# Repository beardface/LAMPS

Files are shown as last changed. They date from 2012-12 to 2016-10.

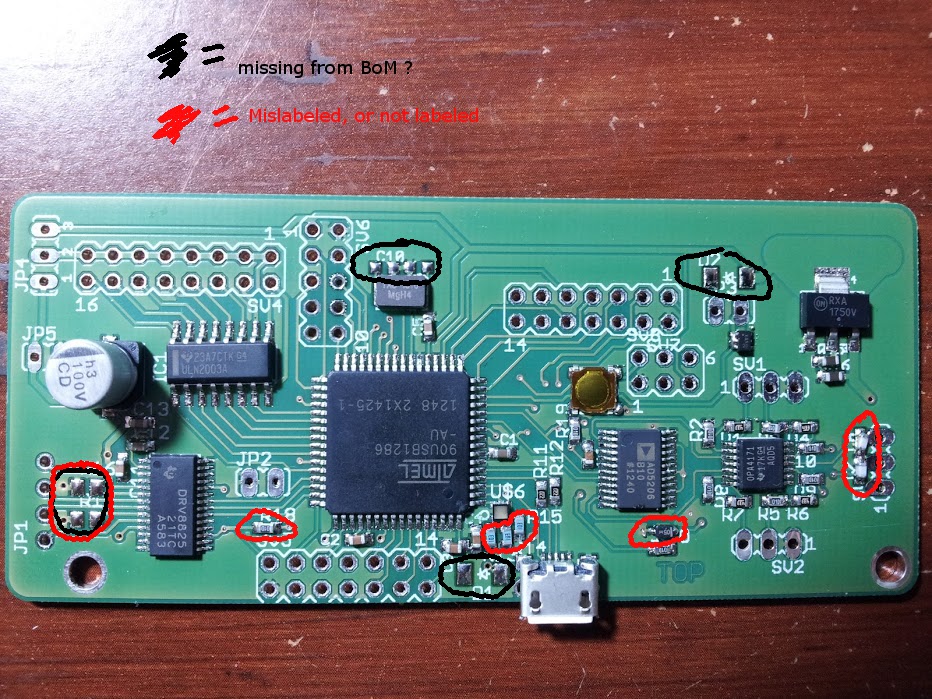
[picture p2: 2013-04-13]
pcb_design/OpenSL_1.0/board_review.jpg

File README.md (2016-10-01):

LAMPS - The Open Hardware SLA Printer
-------------------------------------
LAMPS (Laser Arduino Mega Pololu Shield|SLA Printer) is an open control board and SLA printer design.  The SLA Printer strives to be a low-cost, small footprint (It is only 200mmx350mm!), highly capable SLA Printer. The build platform size is currently 100mmx100mm, but could probably be increased by someone who is motivated to enhance the design.

#License
The schematic for the OpenSL electronics are licensed under the GPL.

The printer and its associated parts are licensed under the Creative Commons Attribution-NonCommercial-ShareAlike 3.0 Unported License.

Basically, use my design all you want! :) But, don't sell it.  If you want an exception, contact me.

#LAMPS Board
LAMPS is the PCB control board that rides on top of an Arduino Mega 2560.  It provides Galvanometer control (Through 12 bit DACs).  It also controls the laser, buttons, Z Stepper Motor (Through Pololu Carrier), End Stops, LEDs, etc...  (It is the Brainz).

Version 1.0 of the LAMPS board has been manufactured and tested... I found a few issues with the board and am currently redesigning and removing a few unnecessary components for 1.1. Release date T.B.D.

#Firmware
The firmware for LAMPS is a fork of Marlin (The best open source RepRap firmware I know of), and can be found here: https://github.com/beardface/Marlin-OpenSL
The firmware is very much an active work-in-progress, and I encourage you to fork, and contribute.

#LAMPS Printer Parts -WARNING... THIS IS NOT UP TO DATE-
All of the parts are available as sketchup (skp) and stl files.

##Printed Parts
* 1x [Laser Mount](https://github.com/beardface/LAMPS/blob/master/parts/lasermount.stl)
* 1x [Mirror Mount](https://github.com/beardface/LAMPS/blob/master/parts/mirrormount.stl)
* 4x [Vibrating Vat Mount](https://github.com/beardface/LAMPS/blob/master/parts/vibrating_vat_mount.stl)
* 1x [Z-Axis Top Mount](https://github.com/beardface/LAMPS/blob/master/parts/z_top_mount.stl)
* 1x [Z-Axis Bottom Mount](https://github.com/beardface/LAMPS/blob/master/parts/z_bottom_mount.stl)
* 1x [Build Platform Mount](https://github.com/beardface/LAMPS/blob/master/parts/platform_mount.stl)
* 1x [Build Stage](https://github.com/beardface/LAMPS/blob/master/parts/build_platform_connector.stl)
* 1x Endstop Mount

##Laser Cut Parts
###Platform
Use 3/16"-1/4" thick acrylic for the platforms.
* 1x [Vat Platform](https://github.com/beardface/LAMPS/blob/master/parts/top_platform.svg)
* 1x [Component Platform](https://github.com/beardface/LAMPS/blob/master/parts/bottom_platform.svg)
* 1x 80mmx80mm 1/4"Acryilc Stage Mount (leftover part from cutting of top_platform)

###VAT
Use 1/4" Clear (Transparent) Acrylic for the VAT!
* 1x [Vat Back](https://github.com/beardface/LAMPS/blob/master/parts/vat_design/vat_back.svg)
* 1x [Vat Front](https://github.com/beardface/LAMPS/blob/master/parts/vat_design/vat_front.svg)
* 1x [Vat Bottom](https://github.com/beardface/LAMPS/blob/master/parts/vat_design/vat_bottom.svg)
* 1x [Vat Handle](https://github.com/beardface/LAMPS/blob/master/parts/vat_design/vat_handle.svg)
* 2x [Vat Sides](https://github.com/beardface/LAMPS/blob/master/parts/vat_design/vat_side.svg)

##Non-Printed Parts
* 1x NEMA 17 Stepper Motor (Low Profile!)
* 2x 8mm Smooth Rod (~260mm)
* 1x 8mm Threaded Rod (~260mm) and 2-M8 nuts
* 4x LM8UU Bearings
* 1x LAMPS Electronics Kit (w/Pololu and 2x endstops)
* 1x LAMPS PCB Build Platform
* 1x LAMPS Musimi 2020 Rail Kit and connectors
  * 4x  350mm 2020 Extrusions w/end tapping holes
  * 11x 160mm 2020 Extrusions
  * 1x  110mm 2020 Extrusion
* 1x LAMPS Enclsoure & Hatch Kit
* 1x 405nm Laser (20mw-150mw) -- Build properties/cure time/etc... vary by laser!
* 1x 3" Square Mirror
* 1x Laser Galvo Set (20kpps) w/power supply
 * Resistance Configuration (Note to Self)
  * AXIS  |  SIZE     | GAIN      | LF         | HF        | LINEAR
  * X     |  4.96Kohm | 4.68 Kohm | 26.36 Kohm | 4.78 Kohm | 1.75 Kohm
  * Y     |  6.1Kohm  | 4.18 Kohm | 26.47 Kohm | 4.37 Kohm | 2.3 Kohm
* 1x +/-12V Power Supply (~1-3Amps)
* USB Cable
* Power Cable
* Screws, Nuts, Wires, Solder, Patience

##Optional (But Useful) Non-Printed Parts
* 1xLCD Screen
* 1xSD Card Reader (and corresponding circuit... T.B.D.)
* 1x Power Switch (110-250VAC), lighted
* 1x Power Terminal (Two combine power into single input)
* 1x 3-Prong Power Jack
 
###LAMPS IS A WORK IN PROGRESS.

##Some words of Caution
* Careful with 110-250VAC, it can --bite-- Seriously Harm you if you aren't careful
* Some 405nm Resins can be toxic while curing- take the appropriate measures to ensure you are working in a well ventelated room

~LAMPS design, details, and parts list are provided without any warranty or gaurantee- this is a community project, so lets work together to solve issues that may arise!

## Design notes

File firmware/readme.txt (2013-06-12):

Firmware can be found at:
http://github.com/Beardface/Marlin-OpenSL

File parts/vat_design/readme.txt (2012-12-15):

==Instructions==
Cut one of every part using 1/4" clear acrylic, except for vat_side.svg... you need two of those.

===Parts===
Vat Bottom (vat_bottom.svg) - Qty 1
Vat Side   (vat_side.svg)   - Qty 2
Vat Back   (vat_back.svg)   - Qty 1
Vat Front  (vat_front.svg)  - Qty 1
Vat Handle (vat_handle.svg) - Qty 1

*Glue all parts together, clamping as necessary.

*Once parts are glued together and vat has dried, use silicon to create a water tight seal on vat inside edges.

*You'll need to apply something (unkown) to the vat floor to prevent cured acrylic from sticking.

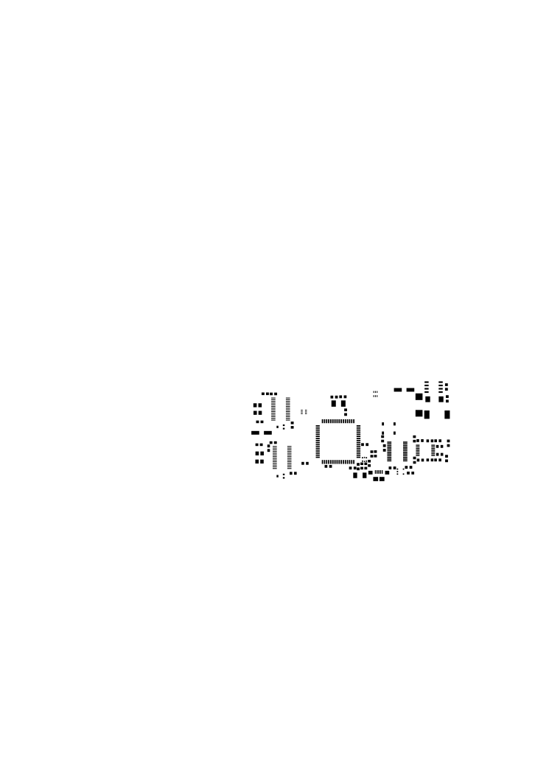
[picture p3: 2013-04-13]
pcb_design/OpenSL_1.0/usbl_stencil.png

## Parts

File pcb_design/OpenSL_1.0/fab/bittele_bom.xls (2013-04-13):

 | Open SL 1.0 – BOM – Pryntech
Item # | Ref Des | Description | Qty | Manufacturer | Mfg Part # | SMD count | THR count | FP count | Link
1 | U$1 | Processor | 1 | Atmel | AT90USB1286 | 1 |  |  | http://www.digikey.de/product-detail/de/AT90USB1286-AU/AT90USB1286-AU-ND/2238141
2 | U$7 U$11 | Stepper motor driver | 2 | Texas Instruments | DRV8825 |  |  | 2 | http://de.mouser.com/ProductDetail/Texas-Instruments/DRV8825PWP/?qs=sGAEpiMZZMvt6eWNl%252b39CONAp7d4Q4UX
3 | R16 R17 R22 R23 | Current sense resistor | 4 | Susumu | RL1220T-R050-J | 4 |  |  | http://www.digikey.de/product-detail/de/RL1220T-R050-J/RL12T.05JCT-ND/567358
4 | U$2 | Digital potentiometer | 1 | Analog Devices | AD5206BRUZ10-RL7 |  |  | 1 | http://www.digikey.de/product-detail/de/AD5206BRUZ10-RL7/AD5206BRUZ10-RL7CT-ND/3727008
5 | U$3 | Quad opamp | 1 | Texas Instruments | OPA4171 |  |  | 1 | http://de.mouser.com/ProductDetail/Texas-Instruments/OPA4171AIPW/
6 | U$4 | Crystal | 1 | TXC | 7A-16.000MAAJ-T | 1 |  |  | http://www.digikey.de/product-detail/de/7A-16.000MAAJ-T/887-1086-1-ND/2118963
7 | LASER, ENDA, ENDB, 24V | Connector screw term | 4 | TE Connectivity | 282834-2 |  | 4 |  | http://de.mouser.com/ProductDetail/TE-Connectivity-AMP/282834-2/
8 | MOTOR-A, MOTOR-B | Connector screw term | 2 | TE Connectivity | 282834-4 |  | 2 |  | http://de.mouser.com/ProductDetail/TE-Connectivity/282834-4/?qs=A%252bip%252bNCYi6Pqom9P%2faHyRQ%3d%3d
9 | +-15V XGAL YGAL | 1x3 0.1” header | 3 | FCI | 68001-203HLF |  | 3 |  | http://de.mouser.com/ProductDetail/FCI/68001-203HLF/
10 | U$40 | Switch regulator | 1 | Maxim | MAX5035BASA/V+ | 1 |  |  | http://de.mouser.com/ProductDetail/Maxim-Integrated/MAX5035BASA-V+/
11 | U$9 U$13 | MOSFET | 2 | Infineon | BSD816SNL6327 |  |  | 2 | http://de.mouser.com/ProductDetail/Infineon-Technologies/BSD816SN-L6327/?qs=sGAEpiMZZMskA%2fTOHXebNu3gKtDta7Pm
12 | U$14 | Linear regulator | 1 | On Semi | CAT6219-330TD-G | 1 |  |  | http://de.mouser.com/Search/ProductDetail.aspx
13 | U$6 | LED | 1 |  | LRTBR98G-R7T5-1+S7U-37+P7 | 1 |  |  | http://de.mouser.com/ProductDetail/Maxim-Integrated/MAX5035BASA-V+/
14 | U$8 U$12 | Potentiometer | 2 |  | PVZ3A103C01B00 | 2 |  |  | http://de.mouser.com/ProductDetail/Murata/PVZ3A103C01B00/?qs=sGAEpiMZZMvygUB3GLcD7pHHMwHWVspDJmsoKyelQV0%3d
15 | FAN, BOOT | 2x1 0.1” header | 2 | FCI | 68001-202H |  | 2 |  | http://de.mouser.com/ProductDetail/FCI/68001-202H/?qs=sGAEpiMZZMtsLRyDR9nM15lq0NThqwkGsPHYSk2petY%3d
16 | U$41 | Inductor | 1 | Bourns | SRU8043-101Y | 1 |  |  | http://www.digikey.de/product-detail/de/SRU8043-101Y/SRU8043-101YCT-ND/2353060
17 | D2 | Diode | 1 | ON Semi | MBRS2040LT3G | 1 |  |  | http://www.digikey.de/product-detail/de/MBRS2040LT3G/MBRS2040LT3GOSCT-ND/918004
18 | AUX2 | 2x5 0.1” header | 1 | FCI | 77313-802-10LF |  | 1 |  | http://de.mouser.com/ProductDetail/FCI/77313-802-10LF/
19 | R2 R3 R5 R8 R9 R10 R18 R19 R21 R24 | Resistor (100K) | 10 | Kamaya | WR06X1003FTL | 8 |  |  | http://de.mouser.com/ProductDetail/Kamaya/WR06X1003FTL/
20 | C14 C32 | Bulk capacitor | 2 | Panasonic | EEE-FPV101XAP | 2 |  |  | http://www.digikey.de/product-detail/de/EEE-FPV101XAP/PCE4554CT-ND/1701053
21 | C31 | Output capacitor | 1 | Kemet | T495D686M010ATE150 | 1 |  |  | http://de.mouser.com/ProductDetail/Kemet/T495D686M010ATE150/
22 | R11 R12 | Resistor (22R) | 2 | Bourns | CR0603-FX-22R0ELF | 2 |  |  | http://de.mouser.com/ProductDetail/Bourns/CR0603-FX-22R0ELF/?qs=sGAEpiMZZMu61qfTUdNhG6LqqFhkr6pU9bwfCpAqbTI%3d
23 | D1 | Diode | 1 | ON Semi | MBR0520LT1G | 1 |  |  | http://www.digikey.de/product-detail/de/MBR0520LT1G/MBR0520LT1GOSCT-ND/917965
24 | R1 R4 R6 R7 R13 R14 R15 | Resistor (43K) | 7 | Bourns (http://de.mouser.com/bourns) | CR0603-FX-4302ELF (http://de.mouser.com/ProductDetail/Bourns/CR0603-FX-4302ELF/) | 7 |  |  | http://de.mouser.com/ProductDetail/Bourns/CR0603-FX-4302ELF/
25 | C3 C18 C19 | MLCC | 3 | TDK | C1608X6S1A106M | 3 |  |  | http://de.mouser.com/ProductDetail/TDK/C1608X6S1A106M/
26 | C2 C4 C5 C6 C7 C8 C11 C13 C15 C17 C20 C29 C30 | MLCC | 13 | TDK | C1608Y5V1H104Z | 13 |  |  | http://de.mouser.com/ProductDetail/TDK/C1608Y5V1H104Z/?qs=sGAEpiMZZMvQvaS66kI3TvHonbvhj0AsH45N8eLStt8%3d
27 | C12 C16 | MLCC (0.01u) | 2 | TDK | CGA5L4C0G2J103J | 2 |  |  | http://de.mouser.com/ProductDetail/TDK/CGA5L4C0G2J103J/?qs=sGAEpiMZZMs5EsmM6MQhfRRHRow8fGba
28 | C1 | MLCC | 1 | Vishay/Vitramon | VJ0603V105MXQPW1BC | 1 |  |  | http://de.mouser.com/ProductDetail/Vishay-Vitramon/VJ0603V105MXQPW1BC/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
29 | U$10 | Push button | 1 | E-Switch | TL3315NF250Q | 1 |  |  | http://www.digikey.de/product-detail/de/TL3315NF250Q/EG4622CT-ND/1870402
30 | AUX1 | 2x7 0.1” header | 2 | FCI | 67997-114HLF |  | 2 |  | http://de.mouser.com/ProductDetail/FCI/67997-114HLF/
31 | ICSP | 2x3 0.1” header | 1 | FCI | 67996-206HLF |  | 1 |  | http://de.mouser.com/ProductDetail/FCI/67996-206HLF/
32 | C9 C10 | MLCC | 2 | Murata | GRM1885C1H180FA01J | 2 |  |  | http://de.mouser.com/ProductDetail/Murata/GRM1885C1H180FA01J/
33 | U$5 | USB connector | 1 | FCI | 10118193-0001LF | 1 |  |  | http://de.mouser.com/Search/ProductDetail.aspx

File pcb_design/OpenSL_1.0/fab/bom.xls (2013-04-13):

Line item | Count | PN | Cost/100 | Cost/ea | Cost/50 | Cost/ea | Cost/25 | Cost/ea | RD | Description | Value | Package | Ratings | Mnft | Source | SMD count | THR count | FP count | LL count | Link
1 | 1 | AT90USB1286 | 503.45 | 5.0345 | 285.68 | 5.7136 | 142.84 | 5.7136 | U$1 | Processor |  | TQFP-64 |  | Atmel | digikey | 1 |  |  |  | http://www.digikey.de/product-detail/de/AT90USB1286-AU/AT90USB1286-AU-ND/2238141
2 | 2 | DRV8825 | 602 | 6.02 | 302 | 6.04 | 208 | 8.32 | U$7 U$11 | Stepper motor driver |  |  |  | Texas Instruments | mouser |  |  | 2 |  | http://de.mouser.com/ProductDetail/Texas-Instruments/DRV8825PWP/?qs=sGAEpiMZZMvt6eWNl%252b39CONAp7d4Q4UX
3 | 4 | RL1220T-R050-J | 53.07 | 0.5307 | 34.12 | 0.6824 | 17.06 | 0.6824 | R16 R17 R22 R23 | Current sense resistor | 0.05R | R0805 | 5% 1/4W | Susumu | digikey | 4 |  |  |  | http://www.digikey.de/product-detail/de/RL1220T-R050-J/RL12T.05JCT-ND/567358
4 | 1 | AD5206BRUZ10-RL7 | 315.89 | 3.1589 | 173.66 | 3.4732 | 86.83 | 3.4732 | U$2 | Digital potentiometer | 10k | TSSOP24 |  | Analog Devices | digikey |  |  | 1 |  | http://www.digikey.de/product-detail/de/AD5206BRUZ10-RL7/AD5206BRUZ10-RL7CT-ND/3727008
5 | 1 | OPA4171 | 112 | 1.12 | 83.5 | 1.67 | 41.75 | 1.67 | U$3 | Quad opamp |  | TSSOP14 |  | Texas Instruments | mouser |  |  | 1 |  | http://de.mouser.com/ProductDetail/Texas-Instruments/OPA4171AIPW/
6 | 1 | 7A-16.000MAAJ-T | 45.02 | 0.4502 | 28.2 | 0.564 | 14.1 | 0.564 | U$4 | Crystal | 16mhz |  | 30ppm, 18pf | TXC | digikey | 1 |  |  |  | http://www.digikey.de/product-detail/de/7A-16.000MAAJ-T/887-1086-1-ND/2118963
7 | 4 | 282834-2 | 312.4 | 3.124 | 156.2 | 3.124 | 78.1 | 3.124 |  | Connector screw term |  |  |  | TE Connectivity | mouser |  | 4 |  |  | http://de.mouser.com/ProductDetail/TE-Connectivity-AMP/282834-2/
8 | 2 | 282834-4 | 109 | 1.09 | 63.5 | 1.27 | 31.75 | 1.27 |  | Connector screw term |  |  |  | TE Connectivity | mouser |  | 2 |  |  | http://de.mouser.com/ProductDetail/TE-Connectivity/282834-4/?qs=A%252bip%252bNCYi6Pqom9P%2faHyRQ%3d%3d
9 | 3 | 68001-203HLF | 20.6 | 0.206 | 10.3 | 0.206 | 5.5 | 0.22 | +-15V XGAL YGAL | 1x3 0.1” header |  |  |  | FCI | mouser |  | 3 |  |  | http://de.mouser.com/ProductDetail/FCI/68001-203HLF/
10 | 1 | MAX5035BASA/V+ | 199 | 1.99 | 99.5 | 1.99 | 68.75 | 2.75 | U$40 | Switch regulator |  |  |  | Maxim | mouser | 1 |  |  |  | http://de.mouser.com/ProductDetail/Maxim-Integrated/MAX5035BASA-V+/
11 | 2 | BSD816SNL6327 | 40.4 | 0.404 | 20.2 | 0.404 | 11.85 | 0.474 | U$9 U$13 | MOSFET |  |  |  | Infineon | mouser |  |  | 2 |  | http://de.mouser.com/ProductDetail/Infineon-Technologies/BSD816SN-L6327/?qs=sGAEpiMZZMskA%2fTOHXebNu3gKtDta7Pm
12 | 1 | CAT6219-330TD-G | 34.6 | 0.346 | 18.15 | 0.363 | 9.08 | 0.3632 | U$14 | Linear regulator |  |  |  | On Semi | mouser | 1 |  |  |  | http://de.mouser.com/Search/ProductDetail.aspx
13 | 1 | LRTBR98G-R7T5-1+S7U-37+P7 | 45.2 | 0.452 | 23.95 | 0.479 | 12.83 | 0.5132 | U$6 | LED |  |  |  |  |  | 1 |  |  |  | http://de.mouser.com/ProductDetail/Maxim-Integrated/MAX5035BASA-V+/
14 | 2 | PVZ3A103C01B00 | 26.2 | 0.262 | 13.1 | 0.262 | 10.5 | 0.42 | U$8 U$12 | Potentiometer |  |  |  |  |  | 2 |  |  |  | http://de.mouser.com/ProductDetail/Murata/PVZ3A103C01B00/?qs=sGAEpiMZZMvygUB3GLcD7pHHMwHWVspDJmsoKyelQV0%3d
15 | 2 | 68001-202H | 10.4 | 0.104 | 5.2 | 0.104 | 2.9 | 0.116 |  | 2x1 0.1” header |  |  |  | FCI | mouser |  | 2 |  |  | http://de.mouser.com/ProductDetail/FCI/68001-202H/?qs=sGAEpiMZZMtsLRyDR9nM15lq0NThqwkGsPHYSk2petY%3d
16 | 1 | SRU8043-101Y | 55.1 | 0.551 | 29.85 | 0.597 | 17.23 | 0.6892 | U$41 | Inductor |  |  |  | Bourns | digikey | 1 |  |  |  | http://www.digikey.de/product-detail/de/SRU8043-101Y/SRU8043-101YCT-ND/2353060
17 | 1 | MBRS2040LT3G | 48 | 0.48 | 23.99 | 0.4798 | 14.72 | 0.5888 | D2 | Diode |  | DO214AA |  | ON Semi | digikey | 1 |  |  |  | http://www.digikey.de/product-detail/de/MBRS2040LT3G/MBRS2040LT3GOSCT-ND/918004
18 | 1 | 77313-802-10LF | 31 | 0.31 | 15.5 | 0.31 | 7.75 | 0.31 |  | 2x5 0.1” header |  |  |  | FCI | mouser |  | 1 |  |  | http://de.mouser.com/ProductDetail/FCI/77313-802-10LF/
19 | 10 | WR06X1003FTL | 7 | 0.07 | 3.5 | 0.07 | 2 | 0.08 | R2 R3 R5 R8 R9 R10 R18 R19 R21 R24 | Resistor | 100k | R0603 | 1.00% | Kamaya | mouser | 8 |  |  |  | http://de.mouser.com/ProductDetail/Kamaya/WR06X1003FTL/
20 | 2 | EEE-FPV101XAP | 88 | 0.88 | 43.99 | 0.8798 | 24.44 | 0.9776 | C14 C32 | Bulk capacitor | 100u | Panasonic D |  | Panasonic | digikey | 2 |  |  |  | http://www.digikey.de/product-detail/de/EEE-FPV101XAP/PCE4554CT-ND/1701053
21 | 1 | T495D686M010ATE150 | 62.7 | 0.627 | 34.65 | 0.693 | 17.33 | 0.6932 | C31 | Output capacitor | 68u | D/7343-31R |  | Kemet | mouser | 1 |  |  |  | http://de.mouser.com/ProductDetail/Kemet/T495D686M010ATE150/
22 | 2 | CR0603-FX-22R0ELF | 2.2 | 0.022 | 2.2 | 0.044 | 2.2 | 0.088 | R11 R12 | Resistor | 22R | R0603 | 1.00% | Bourns | mouser | 2 |  |  |  | http://de.mouser.com/ProductDetail/Bourns/CR0603-FX-22R0ELF/?qs=sGAEpiMZZMu61qfTUdNhG6LqqFhkr6pU9bwfCpAqbTI%3d
23 | 1 | MBR0520LT1G | 15.21 | 0.1521 | 9.78 | 0.1956 | 4.89 | 0.1956 | D1 | Diode |  | SOD-123 |  | ON Semi | digikey | 1 |  |  |  | http://www.digikey.de/product-detail/de/MBR0520LT1G/MBR0520LT1GOSCT-ND/917965
24 | 7 |  | 6.6 | 0.066 | 4.4 | 0.088 | 2.2 | 0.088 | R1 R4 R6 R7 R13 R14 R15 | Resistor | 43k | R0603 | 1.00% |  | mouser | 7
25 | 3 | C1608X6S1A106M | 40.4 | 0.404 | 20.2 | 0.404 | 15 | 0.6 | C3 C18 C19 | MLCC | 10u | C0603 | 10V | TDK | mouser | 3 |  |  |  | http://de.mouser.com/ProductDetail/TDK/C1608X6S1A106M/
26 | 13 | C1608Y5V1H104Z | 6 | 0.06 | 4 | 0.08 | 2 | 0.08 | C2 C4 C5 C6 C7 C8 C11 C13 C15 C17 C20 C29 C30 | MLCC | 0.1u | C0603 | 50V | TDK | mouser | 13 |  |  |  | http://de.mouser.com/ProductDetail/TDK/C1608Y5V1H104Z/?qs=sGAEpiMZZMvQvaS66kI3TvHonbvhj0AsH45N8eLStt8%3d
27 | 2 |  | 6.2 | 0.062 | 3 | 0.06 | 2 | 0.08 | C12 C16 | MLCC | 0.01u | C0603 |  |  |  | 2
28 | 1 | VJ0603V105MXQPW1BC | 90 | 0.9 | 45 | 0.9 | 20 | 0.8 | C1 | MLCC | 1u | C0603 | 10V | Vishay/Vitramon | mouser | 1 |  |  |  | http://de.mouser.com/ProductDetail/Vishay-Vitramon/VJ0603V105MXQPW1BC/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
29 | 1 | TL3315NF250Q | 13.95 | 0.1395 | 7.38 | 0.1476 | 3.83 | 0.1532 | U$10 | Push button |  |  |  | E-Switch | digikey | 1 |  |  |  | http://www.digikey.de/product-detail/de/TL3315NF250Q/EG4622CT-ND/1870402
30 | 2 | 67997-114HLF | 74.4 | 0.744 | 37.2 | 0.744 | 20.2 | 0.808 |  | 2x7 0.1” header |  |  |  | FCI | mouser |  | 2 |  |  | http://de.mouser.com/ProductDetail/FCI/67997-114HLF/
31 | 1 | 67996-206HLF | 15.7 | 0.157 | 8 | 0.16 | 4 | 0.16 |  | 2x3 0.1” header |  |  |  | FCI | mouser |  | 1 |  |  | http://de.mouser.com/ProductDetail/FCI/67996-206HLF/
32 | 2 | GRM1885C1H180FA01J | 6.2 | 0.062 | 3 | 0.06 | 2 | 0.08 | C9 C10 | MLCC | 18pF | C0603 | 10V | Murata | mouser | 2 |  |  |  | http://de.mouser.com/ProductDetail/Murata/GRM1885C1H180FA01J/
33 | 1 | 10118193-0001LF | 24.8 | 0.248 | 12.8 | 0.256 | 6.4 | 0.256 | U$5 | USB connector |  |  |  | FCI | mouser | 1 |  |  |  | http://de.mouser.com/Search/ProductDetail.aspx
34
35
36
total | 80 | 0 | 3022.69 | 30.2269 | 1625.7 | 32.514 | 910.03 | 36.4012 |  |  |  |  |  |  |  | 57 | 15 | 6 | 0

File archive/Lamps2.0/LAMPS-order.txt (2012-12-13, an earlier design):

Order list for C:/Users/Justin/eagle/LAMPS/Lamps2.0/LAMPS.sch
Exported from EAGLE with DesignLink

Quantity	Value	Package	Order code	Manufacturer	Manuf. Code	Availability	Price (from)	Description
1	7906	TO220V	94M7930		KA7906TU	1087	0.279	FAIRCHILD SEMICONDUCTOR - KA7906TU - IC, V REG -6.0V, 7906, TO-220-3
6		1X02	unknown					
4		1X01	unknown					
1	MSTBA2	MSTBA2	71C4161	FARNELL	1757242	351	0.318	PHOENIX CONTACT - 1757242 - PIN HEADER, 2POS, 5.08MM
1	MSTBA4	MSTBA4	unknown					
1	MSTBA3	MSTBA3	71C4162	FARNELL	1757255	211	0.802	PHOENIX CONTACT - 1757255 - TERMINAL BLOCK, PCB, 3 POS
4		1X04	unknown					
2	M04X2	2X4	unknown					
3	0.1uF	C2.5-2	unknown					
1	100nF	C0805	unknown					
2	1uF	C2.5-2	unknown					
2	100uF	153CLV-0605	unknown					
2	1N4004	DO41-10	unknown					
1	MFR500	MFR500	unknown					
5		3PIN-HEADER	unknown					
1	7805TV	TO220V	unknown					
1	TLV5618	SOCKET-08	76C8920	TEXAS INSTRUMENT CONNECTORS	TLV5618AIP	13	7.52	TEXAS INSTRUMENTS - TLV5618AIP - IC, DAC, 12BIT, 93KSPS, DIP-8
2	TL082P	DIL08	unknown					
1	7806TV	TO220V	unknown					
1		2X03	unknown					
1		2X05	unknown					
3		CHIP-LED0805	unknown					
2	STP55NF06L	TO220BV	63J7168	INTERNATIONAL RECTIFIER(IR)	IRF1010EZPBF	2723	0.848	INTERNATIONAL RECTIFIER - IRF1010EZPBF - N CHANNEL MOSFET, 60V, 75A TO-220AB
1	20k	B25P	unknown					
7	100k	R0805	unknown					
3	1k	B25P	unknown					
5	10k	R0805	unknown					
3	1K	R0805	unknown					
1	10r	R0805	unknown					
1	10r	M0805	unknown					
4	200k	R0805	unknown					
2	4.7K	R0805	unknown					
2	1.8K	R0805	unknown					
1		B3F-31XX	unknown					
2	THAT1646	THAT1646	50M5186		THAT1646P08-U	1	3.39	THAT CORPORATION - THAT1646P08-U - IC, BALANCED LINE DRIVER, DIP-8
1	A4988BREAKOUT	A4988BREAKOUT	unknown					
1	ARDUINO_MEGA_SHIELD	ARDUINO_MEGA_SHIELD	unknown

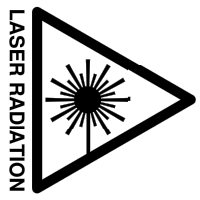
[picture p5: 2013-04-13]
parts/OpenSL/LaserCut/LC_LaserMount/laser_warning_90.png

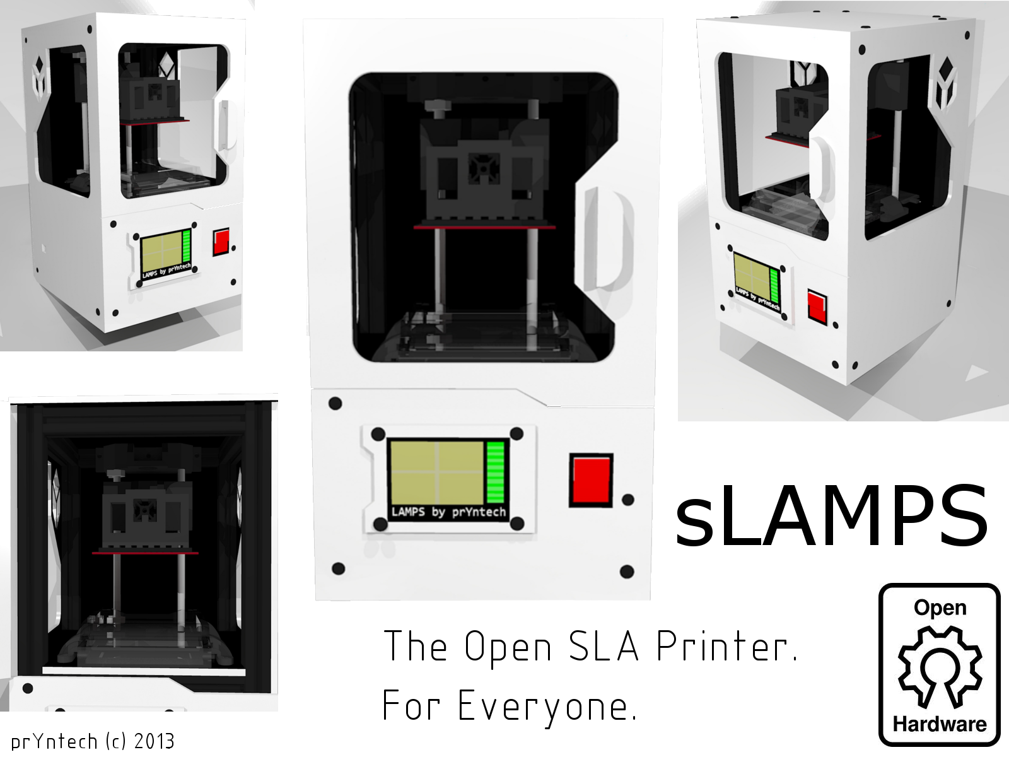
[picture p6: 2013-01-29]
parts/rendering/sLAMPS_Flyer.png

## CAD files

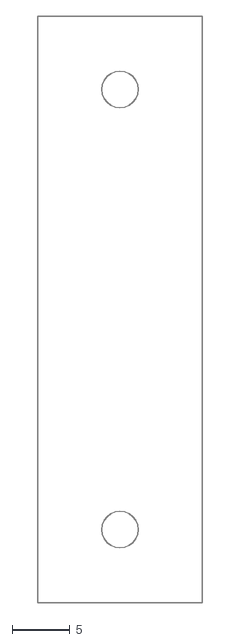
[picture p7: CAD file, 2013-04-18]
parts/2.0_plastic/vat_mount_new.dxf
14.2 x 50.8

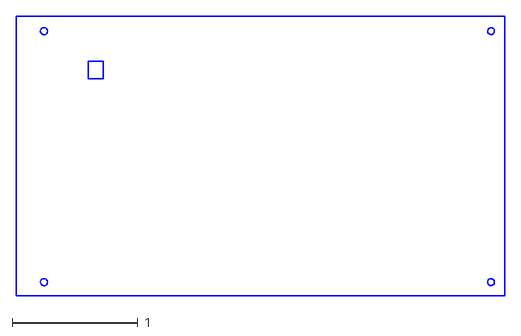
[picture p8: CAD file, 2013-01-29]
parts/case_design/dxf/clear_window/clear_side_window_two.dxf
3.89 x 2.22

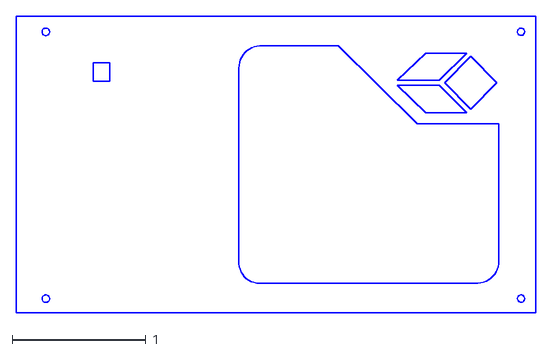
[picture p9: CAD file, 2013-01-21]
parts/case_design/dxf/left_side.dxf
3.89 x 2.22

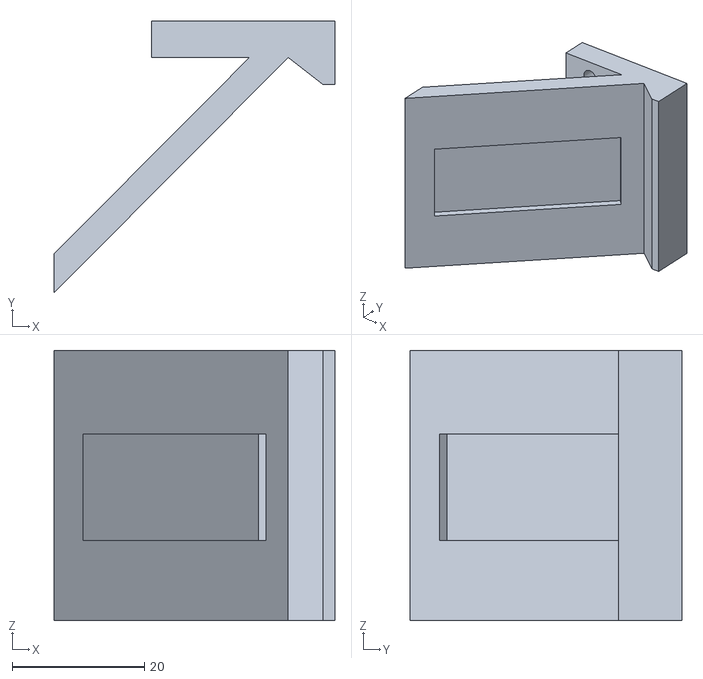
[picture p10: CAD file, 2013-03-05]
parts/Mirror_Mount.stl
42.5 x 41.1 x 40.9

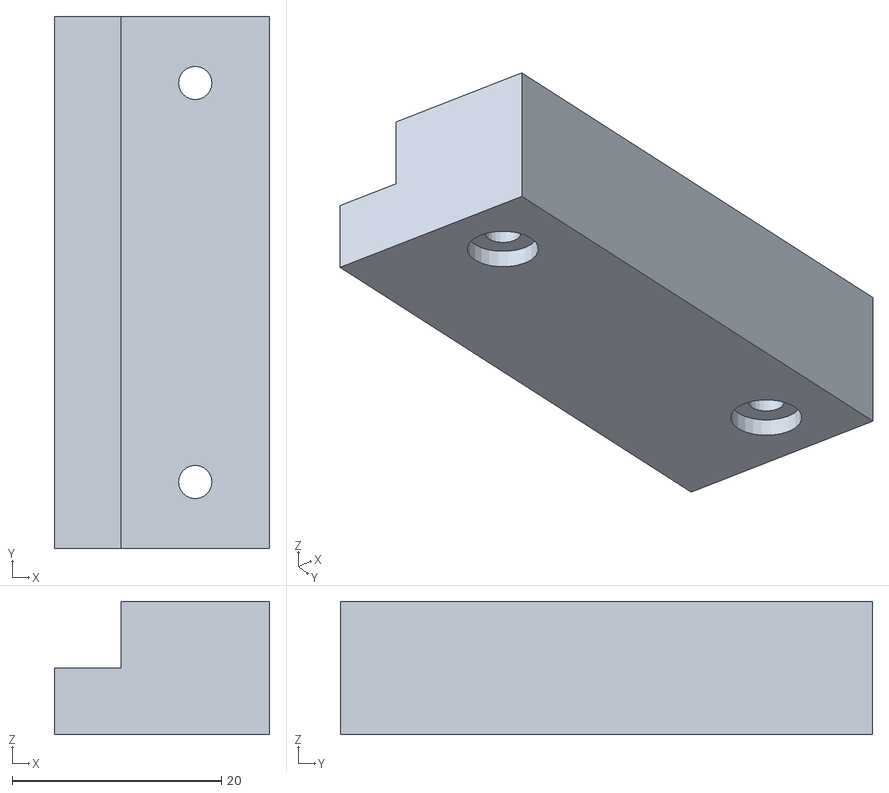
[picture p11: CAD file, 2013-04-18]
parts/OpenSL/3DPrinted/vat_mount.stl
20.5 x 50.8 x 12.7

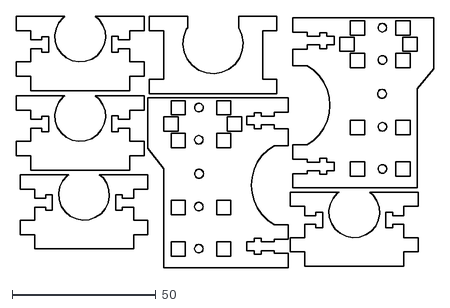
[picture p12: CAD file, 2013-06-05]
parts/OpenSL/LaserCut/DXF/laser_mount.DXF
145.2 x 87.5

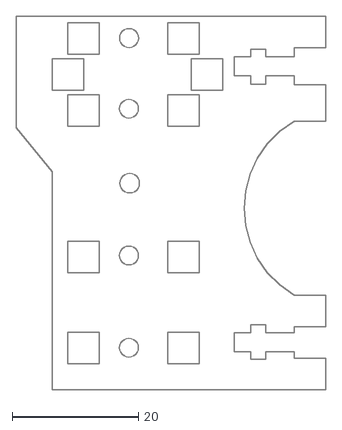
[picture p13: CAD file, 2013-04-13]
parts/OpenSL/LaserCut/LC_LaserMount/laser_mount_3.dxf
49.0 x 59.2

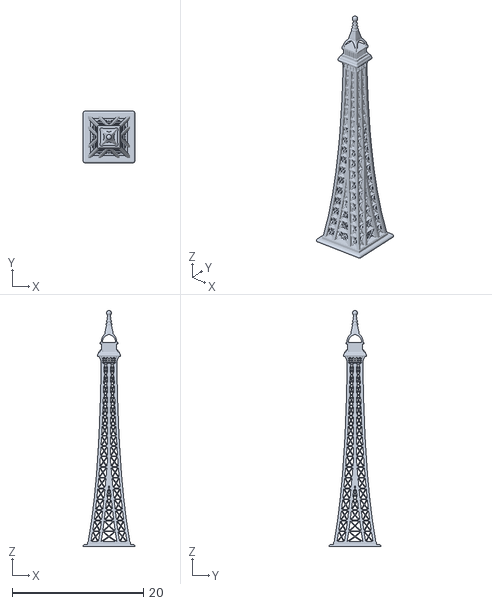
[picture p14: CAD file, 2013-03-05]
parts/tests/EiffelTower_top.stl
7.87 x 7.87 x 36.0

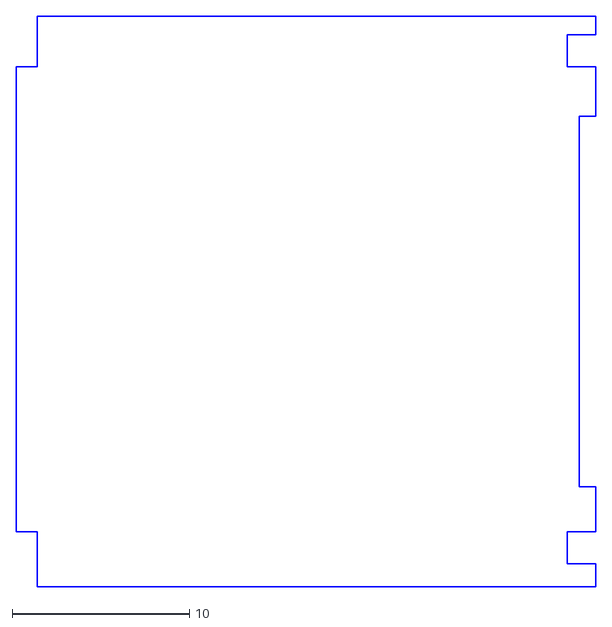
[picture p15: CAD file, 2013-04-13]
parts/vat_design/vat_bottom_test_2.dxf
32.7 x 32.2

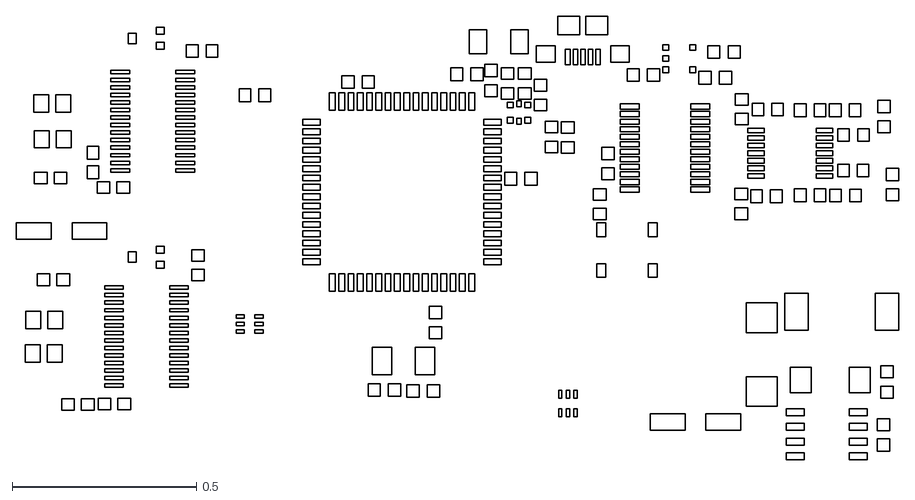
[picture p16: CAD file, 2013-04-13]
pcb_design/OpenSL_1.0/usb3l.dxf
2.39 x 1.20

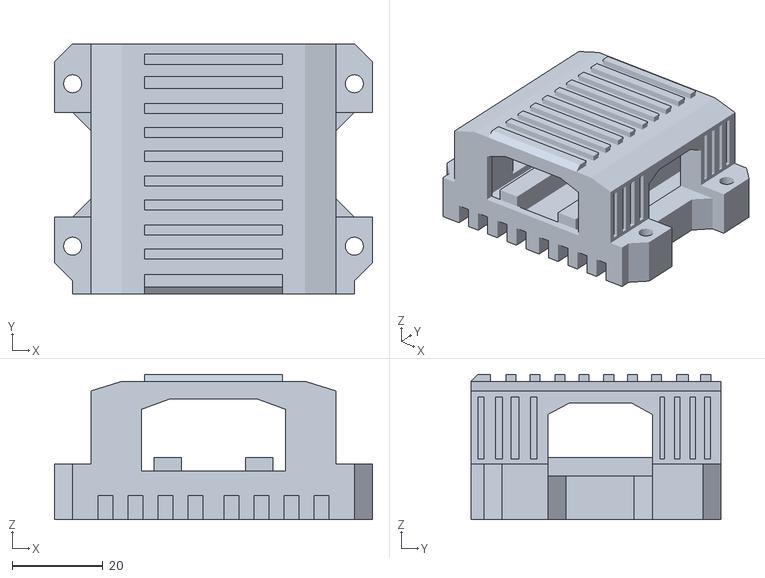
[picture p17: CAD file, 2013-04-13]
parts/2.0_plastic/platform_head.stl
70.1 x 55.2 x 32.1

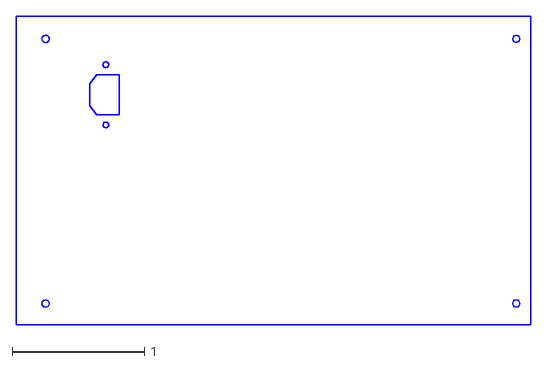
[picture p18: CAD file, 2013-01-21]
parts/case_design/dxf/back.dxf
3.89 x 2.33

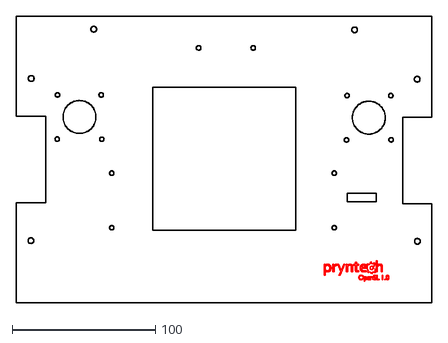
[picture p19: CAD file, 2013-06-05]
parts/OpenSL/LaserCut/DXF/top_platform.DXF
290.1 x 200.0

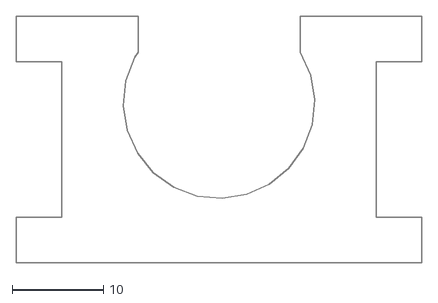
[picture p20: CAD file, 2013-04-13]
parts/OpenSL/LaserCut/LC_LaserMount/laser_mount_2.dxf
44.4 x 27.0

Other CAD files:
parts/tests/vat_adherence_30mm_square.stl
parts/vat_design/vat_bottom_test.dxf
parts/vat_mount.stl
parts/2.0_plastic/laser_mount_2.0.stl
parts/2.0_plastic/platform_base.stl
parts/2.0_plastic/vat_mount_new.skp
parts/Archive/Build_Platform.stl
parts/Archive/LaserAndPrinted/DXF/bottom_platform.DXF
parts/Archive/LaserAndPrinted/DXF/z_mount_left.DXF
parts/Archive/LaserAndPrinted/DXF/z_mount_right.DXF
parts/Archive/LaserAndPrinted/LC_LaserMount/laser_mount_1.dxf
parts/Archive/LaserAndPrinted/laser_mount_2.0.stl
parts/Archive/LaserAndPrinted/platform_base.stl
parts/Archive/LaserAndPrinted/vat_mount_new.skp
parts/Archive/Laser_Mount.stl
parts/Archive/Laser_Mount_Iris.stl
parts/Archive/Vat/vat_back.dxf
parts/Archive/Vat/vat_bottom.dxf
parts/Archive/Vat/vat_bottom_test.dxf
parts/Archive/Vat/vat_front.dxf
parts/Archive/Vat/vat_handle.dxf
parts/Archive/Vat/vat_side.dxf
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

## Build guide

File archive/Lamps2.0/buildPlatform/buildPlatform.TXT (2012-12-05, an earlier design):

%
M48
M72
T01C0.0630
T02C0.0866
%
T01
X1164Y3133
X3133Y1164
X5101Y1164
X7070Y1164
X11991Y1164
X13960Y1164
X15928Y1164
X19865Y1164
X21834Y1164
X23802Y1164
X28723Y1164
X30692Y1164
X32660Y1164
X34629Y3133
X34629Y5101
X34629Y7070
X34629Y11991
X34629Y13960
X34629Y15928
X34629Y19865
X34629Y21834
X34629Y23802
X34629Y28723
X34629Y30692
X34629Y32660
X32660Y34629
X30692Y34629
X28723Y34629
X23802Y34629
X21834Y34629
X19865Y34629
X15928Y34629
X13960Y34629
X11991Y34629
X7070Y34629
X5101Y34629
X3133Y34629
X1164Y32660
X1164Y30692
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

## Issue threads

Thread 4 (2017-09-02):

Purchase hardware

superdave42, 2017-09-02:
Is there any way to purchase this assembled. Just the DAC interface board?

DonVitosurf, 2018-01-16:
I would also like to buy it.

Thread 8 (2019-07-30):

about the STL modle and data in www.pryntech.com

BigYuanHead, 2019-07-30:
hello, I have great interest in this project, but emmmm....unfortunately, I can just get limited information in github, like PCB and its firmware, could you please send me more losed data, such as its assemble guide and STL model...... so that I can complete this machine?? thank you ^-^

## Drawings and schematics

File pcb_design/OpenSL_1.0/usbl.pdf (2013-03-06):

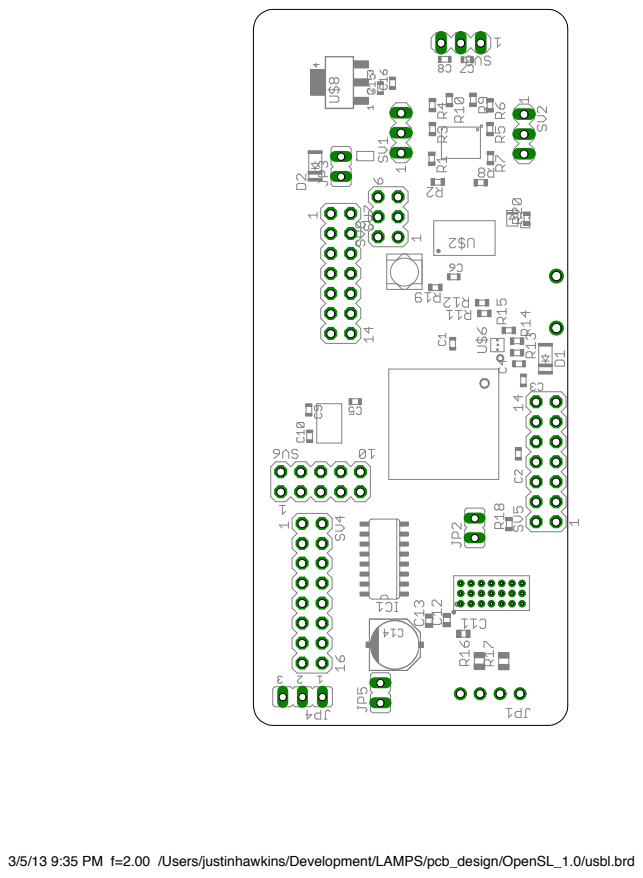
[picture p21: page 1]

3/5/13 9:35 PM f=2.00 /Users/justinhawkins/Development/LAMPS/pcb_design/OpenSL_1.0/usbl.brd

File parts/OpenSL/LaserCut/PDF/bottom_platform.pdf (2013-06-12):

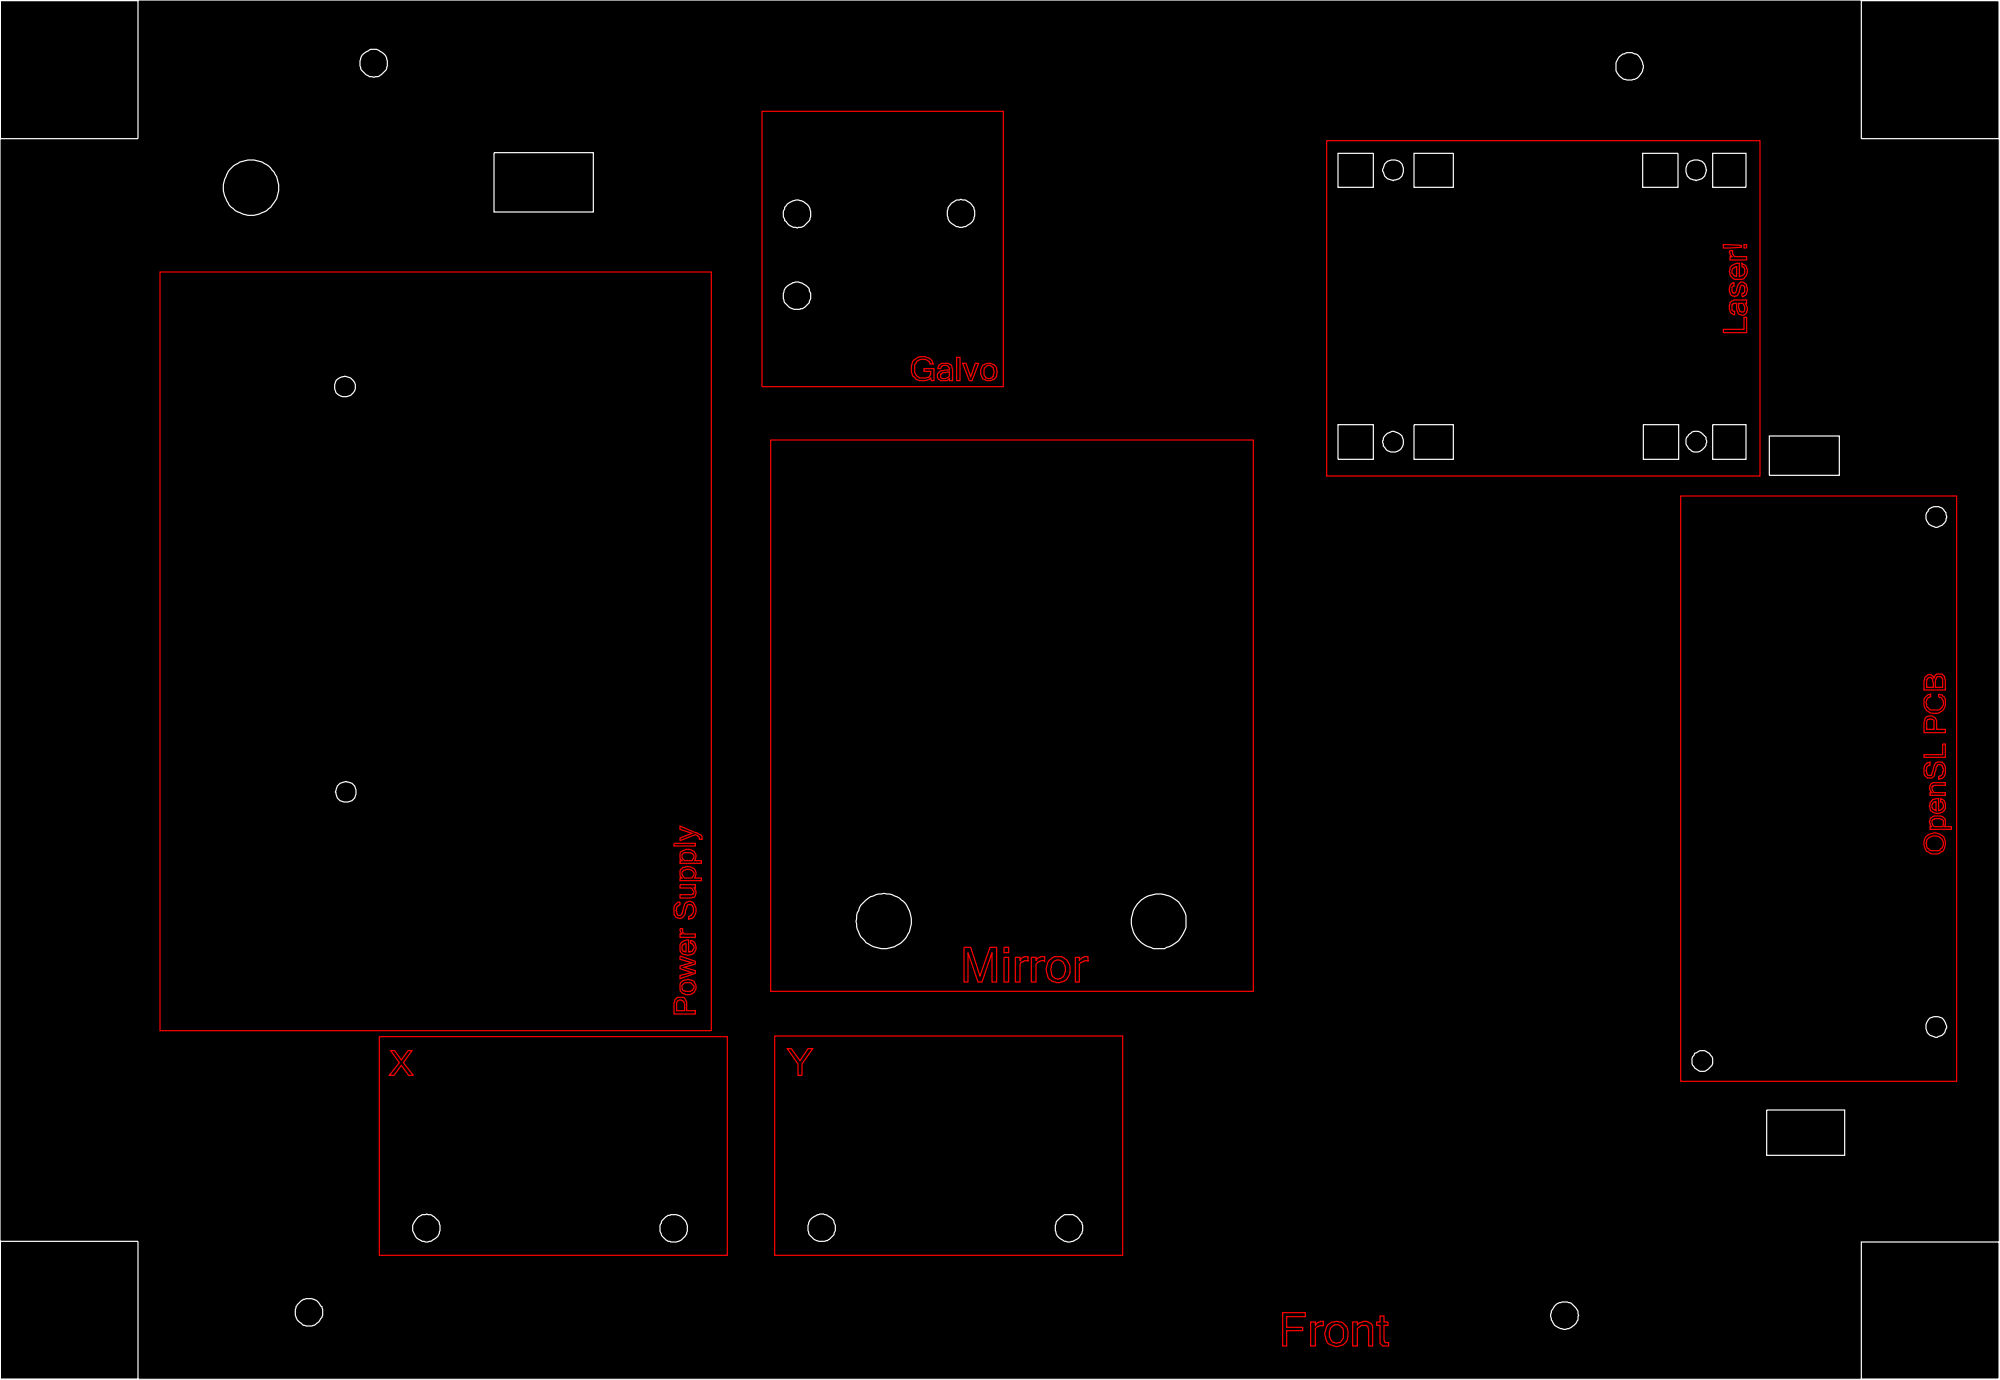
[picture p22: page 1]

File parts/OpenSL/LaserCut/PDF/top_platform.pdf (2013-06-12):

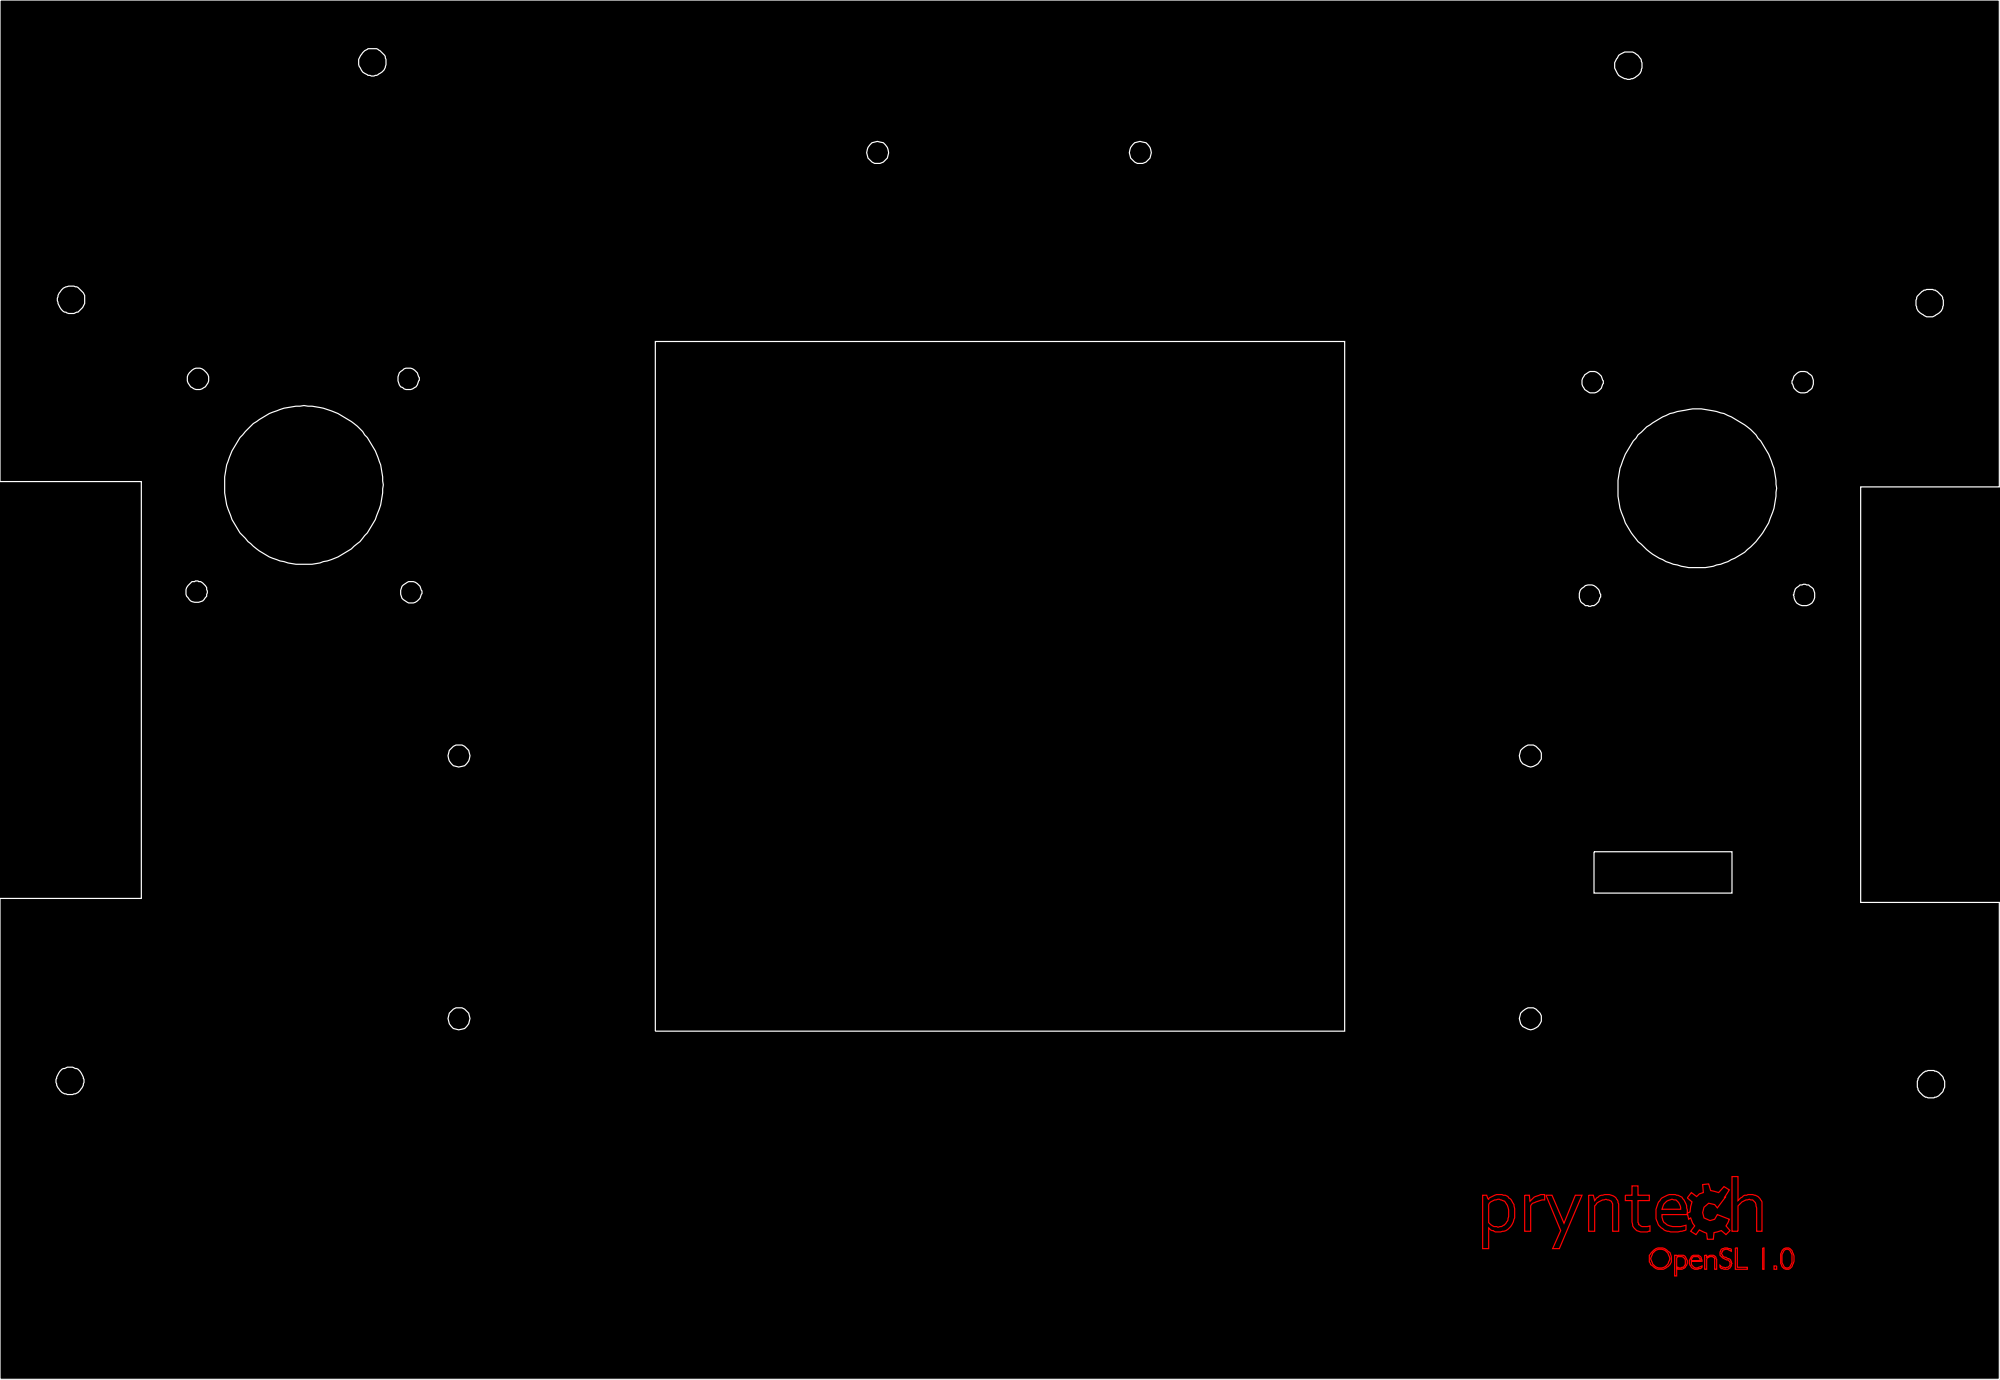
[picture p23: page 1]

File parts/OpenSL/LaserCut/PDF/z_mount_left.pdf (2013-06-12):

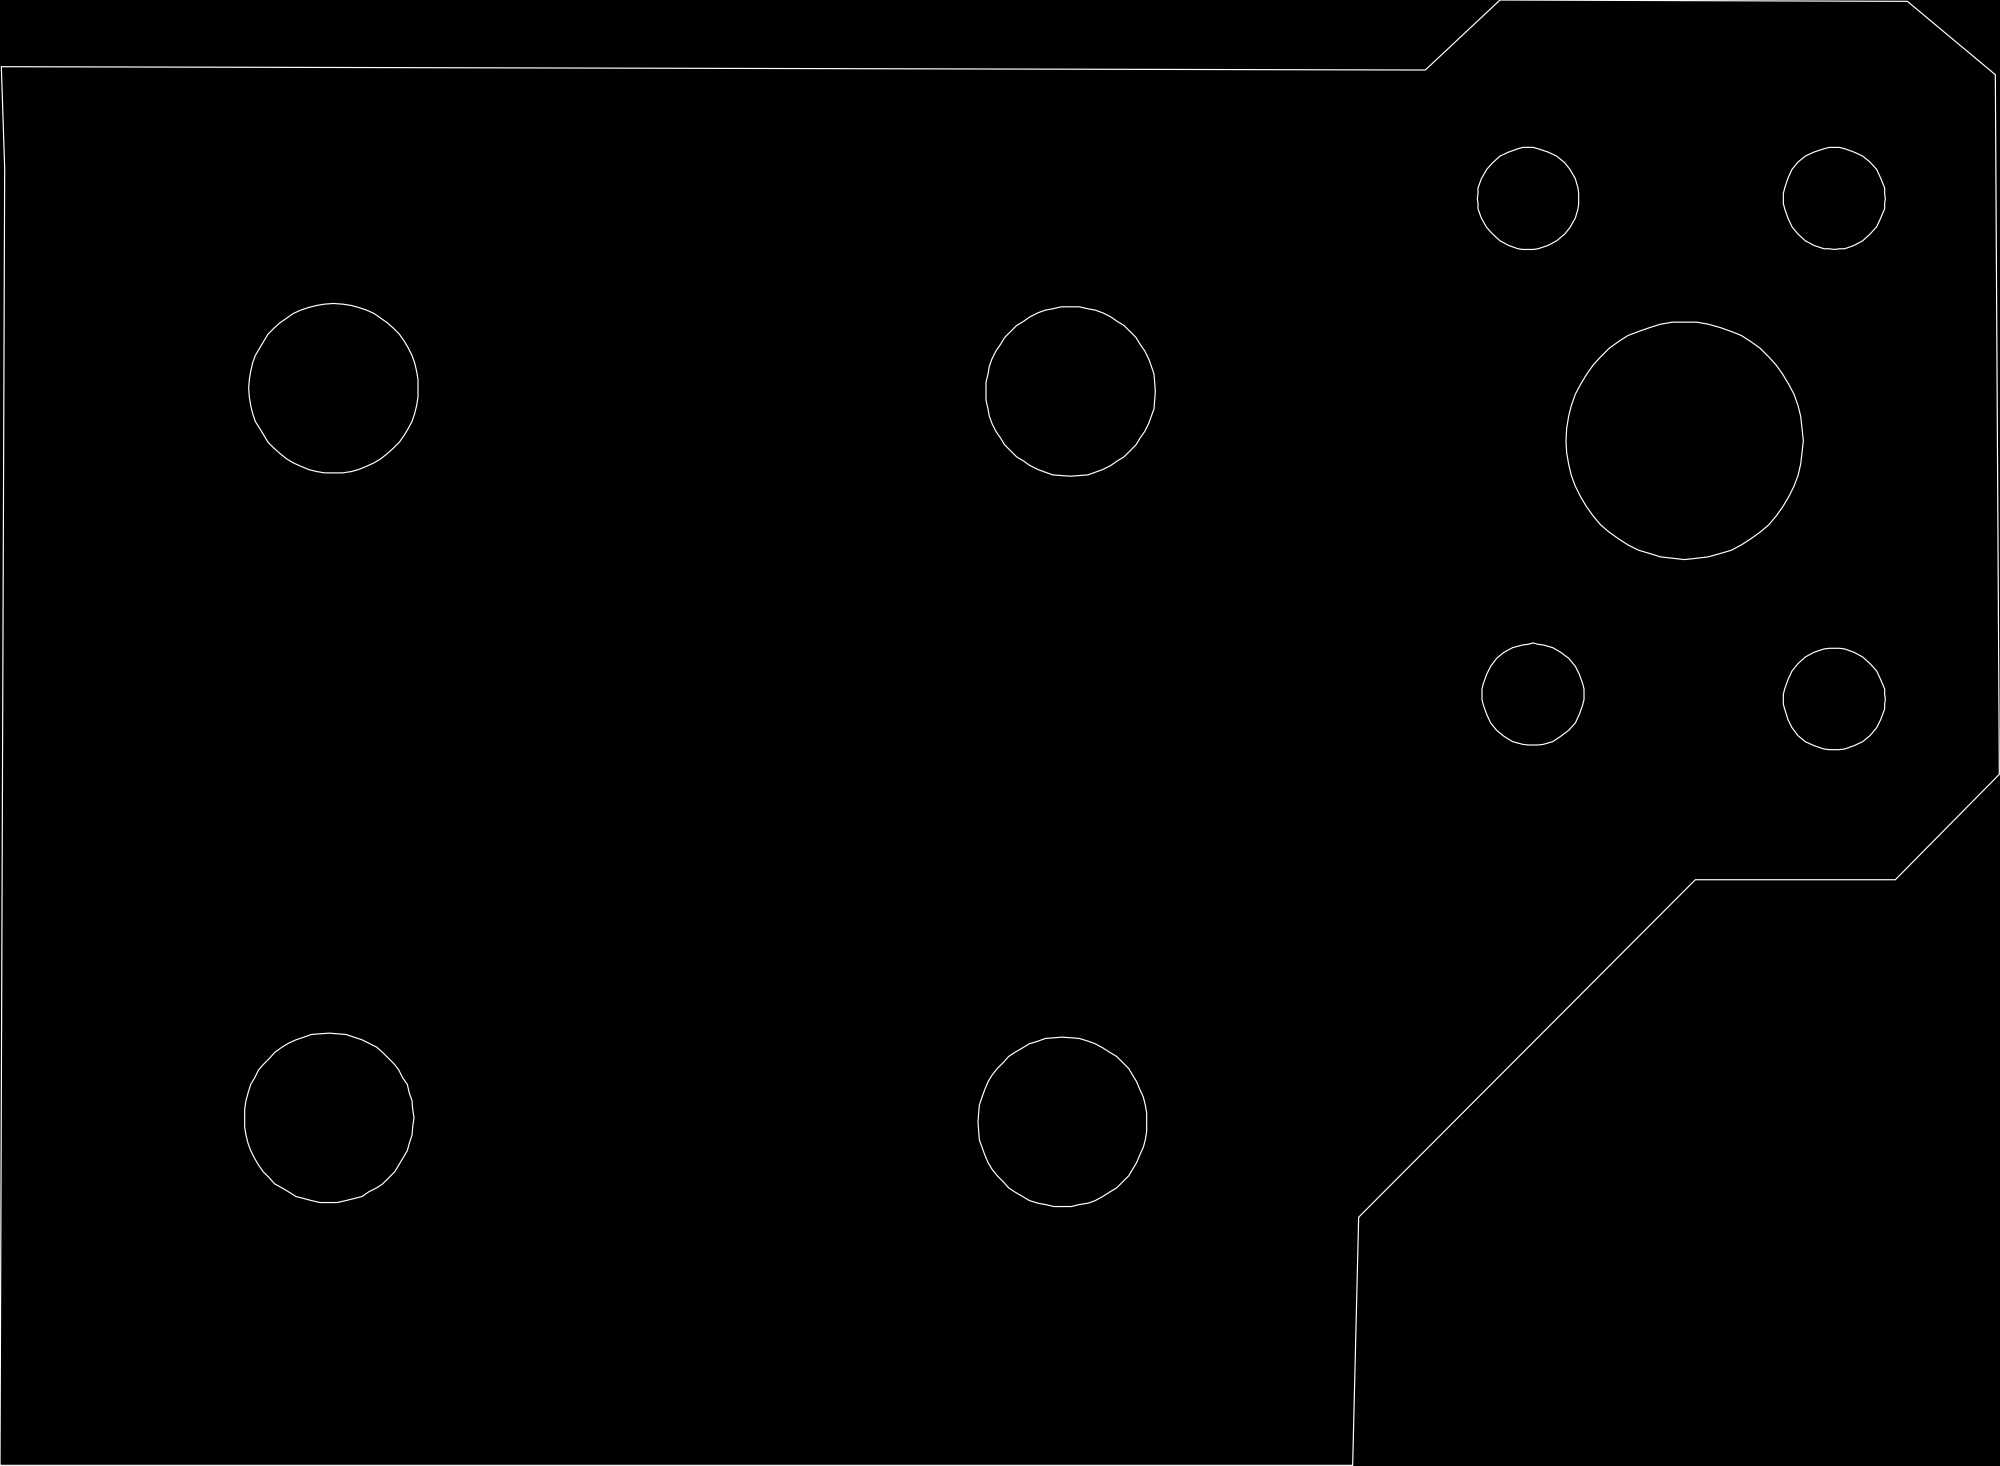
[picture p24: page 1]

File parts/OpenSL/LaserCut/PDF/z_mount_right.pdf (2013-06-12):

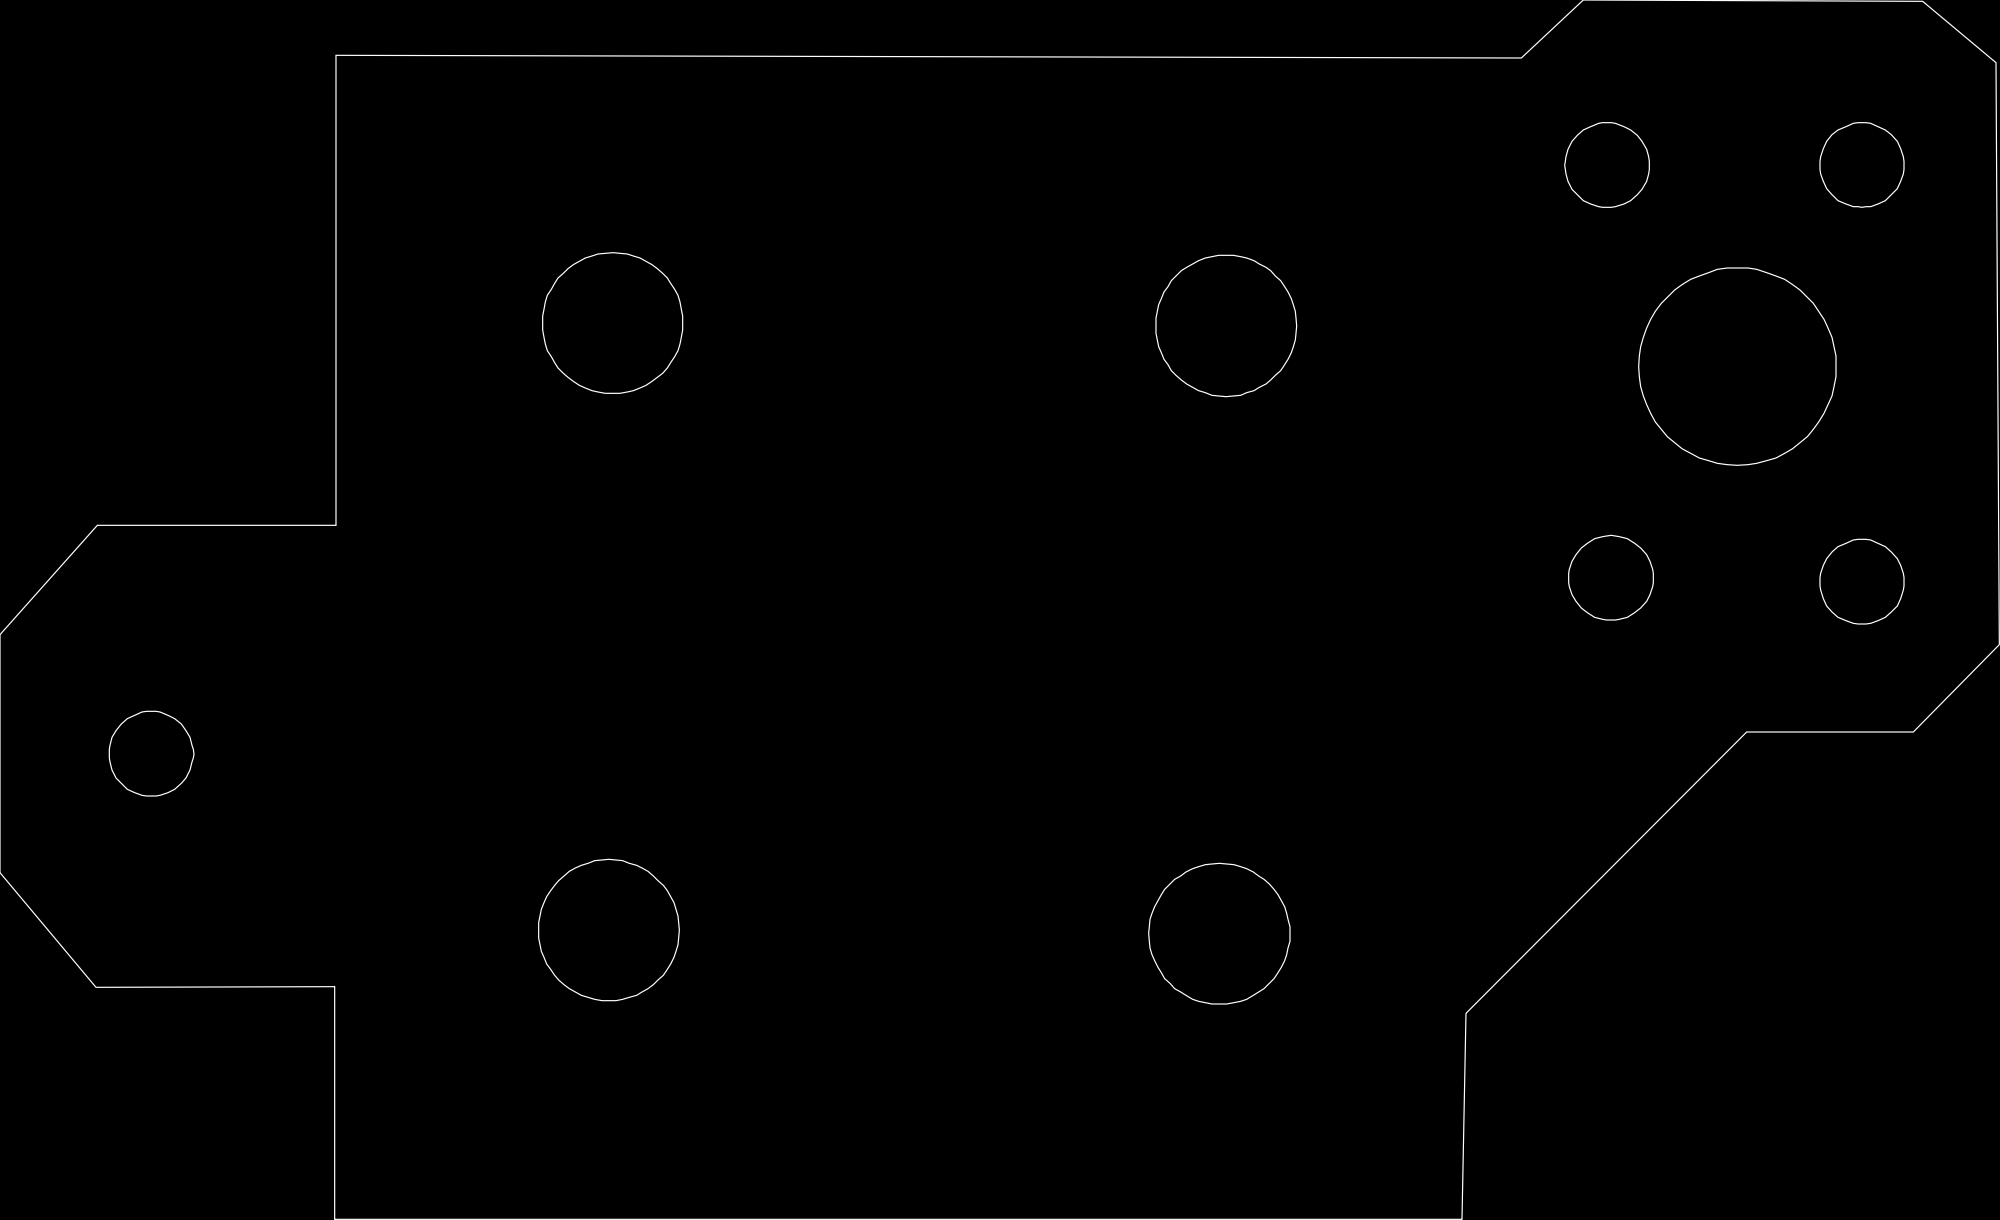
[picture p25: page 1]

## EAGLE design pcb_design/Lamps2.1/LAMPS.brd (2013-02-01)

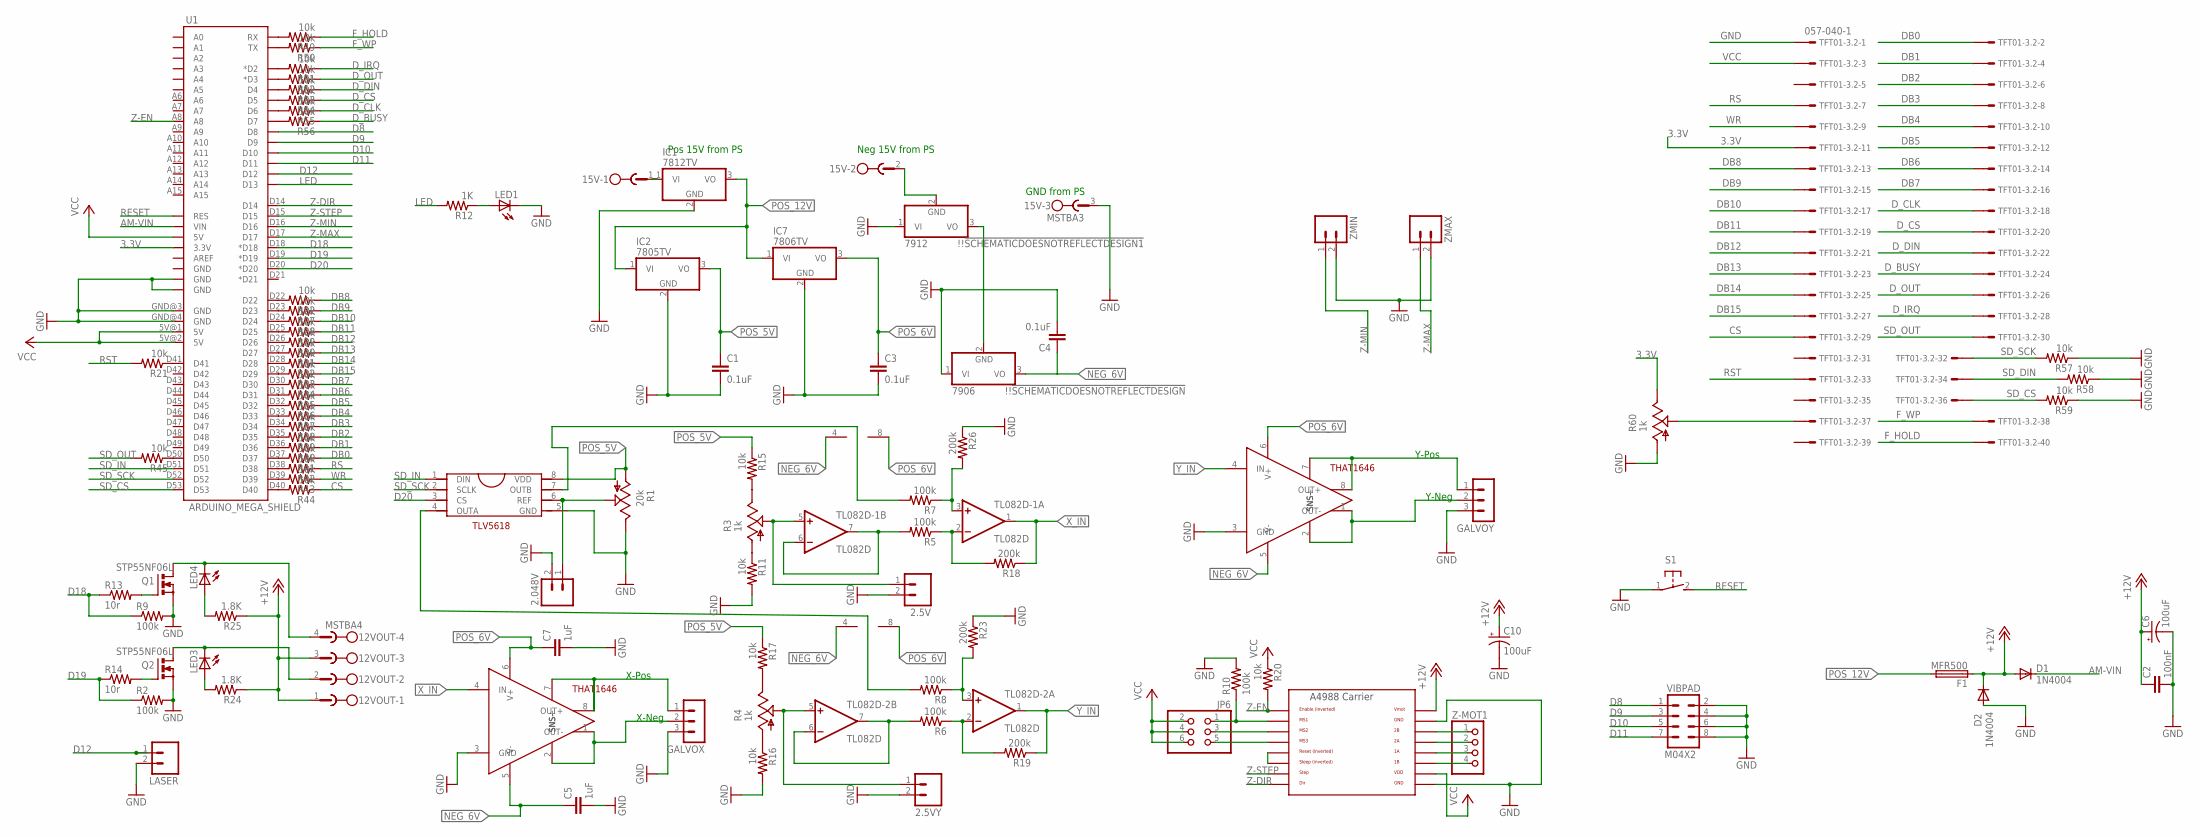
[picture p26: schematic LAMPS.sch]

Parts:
2.5V, 2.5VY, 2.048V: M02PTH; 1X02
12VOUT: MSTBA4
15V: MSTBA3; MPN 1757255
!!!SCHEMATICDOESNOTREFLECTDESIGN: 7906; TO220V; MPN KA7906TU
!!!SCHEMATICDOESNOTREFLECTDESIGN1: 7912; TO220V; MPN KA7906TU
C1, C3, C4: 0.1uF; C2.5-2
C2: 100nF; C0805
C5, C7: 1uF; C2.5-2
C6, C10: 100uF; 153CLV-0605
D1, D2: 1N4004; DO41-10
F1: MFR500
GALVOX: 3PIN-HEADER
GALVOY: 3PIN-HEADER
IC1: 7812TV; TO220V
IC2: 7805TV; TO220V
IC7: 7806TV; TO220V
JP6: PINHD-2X3; 2X03
LASER: M02PTH; 1X02
LED1, LED3, LED4: LEDCHIP-LED0805; CHIP-LED0805
Q1, Q2: STP55NF06L; TO220BV; MPN IRF1010EZPBF
R1: 20k; B25P
R2, R5, R6, R7, R8, R9, R10: 100k; R0805
R3, R4, R60: 1k; B25P
R11, R15, R16, R17, R20, R21, R22, R27, R28, R29, R30, R31, R32, R33, R34, R35, R36, R37, R38, R39, R40, R41, R42, R43, R44, R45, R49, R50, R51, R52, R53, R54, R55, R56, R57, R58, R59: 10k; R0805
R12: 1K; R0805
R13: 10r; R0805
R14: 10r; M0805
R18, R19, R23, R26: 200k; R0805
R24, R25: 1.8K; R0805
S1: 31-XX; B3F-31XX
TFT01-3.2: 057-040-1
TL082D-1, TL082D-2: TL082D; SO08
U1: ARDUINO_MEGA_SHIELD
U$1, U$4: THAT1646; MPN THAT1646P08-U
U$2: THAT1646SMD; TLV5618
U$8: A4988BREAKOUT
VIBPAD: M04X2; 2X4
Z-MOT1: PINHD-1X4; 1X04
ZMAX: M02PTH; 1X02
ZMIN: M02PTH; 1X02

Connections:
3.3V: R60.E, TFT01-3.2.11, U1.3.3V
+12V: 12VOUT.1, 12VOUT.3, C2.1, C6.+, C10.+, D1.A, D2.C, F1.1, R24.1, R25.1, U$8.VMOT
AM-VIN: D1.C, U1.VIN
CS: R44.1, TFT01-3.2.29
D8: U1.D8, VIBPAD.1
D9: U1.D9, VIBPAD.3
D10: U1.D10, VIBPAD.5
D11: U1.D11, VIBPAD.7
D12: LASER.1, U1.D12
D18: R9.1, R13.1, U1.D18 (*D18)
D19: R2.1, R14.1, U1.D19 (*D19)
D20: U1.D20 (*D20), U$2.3 (CS)
DB0: R41.1, TFT01-3.2.2
DB1: R40.1, TFT01-3.2.4
DB2: R39.1, TFT01-3.2.6
DB3: R38.1, TFT01-3.2.8
DB4: R37.1, TFT01-3.2.10
DB5: R36.1, TFT01-3.2.12
DB6: R35.1, TFT01-3.2.14
DB7: R34.1, TFT01-3.2.16
DB8: R22.1, TFT01-3.2.13
DB9: R27.1, TFT01-3.2.15
DB10: R28.1, TFT01-3.2.17
DB11: R29.1, TFT01-3.2.19
DB12: R30.1, TFT01-3.2.21
DB13: R31.1, TFT01-3.2.23
DB14: R32.1, TFT01-3.2.25
DB15: R33.1, TFT01-3.2.27
D_BUSY: R56.1, TFT01-3.2.24
D_CLK: R55.1, TFT01-3.2.18
D_CS: R54.1, TFT01-3.2.20
D_DIN: R53.1, TFT01-3.2.22
D_IRQ: R51.1, TFT01-3.2.28
D_OUT: R52.1, TFT01-3.2.26
F_HOLD: R49.1, TFT01-3.2.40
F_WP: R50.1, TFT01-3.2.38
GND: 2.5V.2, 2.5VY.2, 2.048V.2, 15V.3, !!!SCHEMATICDOESNOTREFLECTDESIGN.1 (VI), !!!SCHEMATICDOESNOTREFLECTDESIGN1.1 (VI), C1.2, C2.2, C3.2, C4.2, C5.2, C6.-, C7.2, C10.-, GALVOX.3, GALVOY.3, IC1.2 (GND), IC2.2 (GND), IC7.2 (GND), LASER.2, LED1.C, Q1.S, Q2.S, R1.E, R2.2, R9.2, R10.2, R11.2, R16.2, R23.1, R26.1, R57.1, R58.1, R59.1, R60.A, S1.1, TFT01-3.2.1, U1.GND@0 (GND), U1.GND@1 (GND), U1.GND@3 (GND), U1.GND@4 (GND), U$1.3 (GND), U$2.5 (GND), U$4.3 (GND), U$8.GND, U$8.GND@0 (GND), VIBPAD.2, VIBPAD.4, VIBPAD.6, VIBPAD.8, ZMAX.2, ZMIN.2
GND_0: D2.A
LED: R12.2, U1.D13
unnamed: 12VOUT.2, LED3.C, Q2.D
unnamed: R21.1, U1.D41
unnamed: !!!SCHEMATICDOESNOTREFLECTDESIGN.2 (GND), !!!SCHEMATICDOESNOTREFLECTDESIGN1.3 (VO)
unnamed: R4.A, R16.1
unnamed: R4.E, R17.2
unnamed: 2.048V.1, R1.S, U$2.6 (REF)
unnamed: 12VOUT.4, LED4.C, Q1.D
unnamed: R3.A, R11.1
unnamed: R3.E, R15.2
unnamed: 2.5VY.1, R4.S, TL082D-2.5 (+IN)
unnamed: 2.5V.1, R3.S, TL082D-1.5 (+IN)
unnamed: GALVOX.2, U$1.1 (OUT-), U$1.2 (SNS-)
unnamed: GALVOX.1, U$1.7 (SNS+), U$1.8 (OUT+)
unnamed: R5.2, TL082D-1.6 (-IN), TL082D-1.7 (OUT)
unnamed: R5.1, R18.2, TL082D-1.2 (-IN)
unnamed: R7.2, U$2.7 (OUTB)
unnamed: R7.1, R26.2, TL082D-1.3 (+IN)
unnamed: R6.2, TL082D-2.6 (-IN), TL082D-2.7 (OUT)
unnamed: R22.2, U1.D22
unnamed: R6.1, R19.2, TL082D-2.2 (-IN)
unnamed: R8.2, U$2.4 (OUTA)
unnamed: R8.1, R23.2, TL082D-2.3 (+IN)
unnamed: R27.2, U1.D23
unnamed: GALVOY.2, U$4.1 (OUT-), U$4.2 (SNS-)
unnamed: GALVOY.1, U$4.7 (SNS+), U$4.8 (OUT+)
unnamed: R28.2, U1.D24
unnamed: R29.2, U1.D25
unnamed: R30.2, U1.D26
unnamed: R31.2, U1.D27
unnamed: R32.2, U1.D28
unnamed: R33.2, U1.D29
unnamed: R34.2, U1.D30
unnamed: R35.2, U1.D31
unnamed: R36.2, U1.D32
unnamed: R37.2, U1.D33
unnamed: R38.2, U1.D34
unnamed: JP6.3, U$8.MS2
unnamed: U$8.RST, U$8.SLP (SLEEP)
unnamed: JP6.5, U$8.MS3
unnamed: JP6.1, R10.1, U$8.MS1
unnamed: U$8.2B, Z-MOT1.1
unnamed: U$8.2A, Z-MOT1.2
unnamed: U$8.1A, Z-MOT1.3
unnamed: U$8.1B, Z-MOT1.4
unnamed: LED3.A, R24.2
unnamed: LED1.A, R12.1
unnamed: Q2.G, R14.2
unnamed: Q1.G, R13.2
unnamed: R39.2, U1.D35
unnamed: LED4.A, R25.2
unnamed: R40.2, U1.D36
unnamed: R41.2, U1.D37
unnamed: R42.2, U1.D38
unnamed: R43.2, U1.D39
unnamed: R44.2, U1.D40
unnamed: R45.1, U1.D50
unnamed: 15V.1, IC1.1 (VI)
unnamed: 15V.2, !!!SCHEMATICDOESNOTREFLECTDESIGN1.2 (GND)
unnamed: R49.2, U1.RX
unnamed: R50.2, U1.TX
unnamed: R51.2, U1.D2 (*D2)
unnamed: R52.2, U1.D3 (*D3)
unnamed: R53.2, U1.D4
unnamed: R54.2, U1.D5
unnamed: R55.2, U1.D6
unnamed: R56.2, U1.D7
unnamed: R60.S, TFT01-3.2.37
NEG_6V: !!!SCHEMATICDOESNOTREFLECTDESIGN.3 (VO), C4.1, C5.1, TL082D-1.4 (V-), TL082D-2.4 (V-), U$1.5 (V-)
POS_5V: C1.1, IC2.3 (VO), R1.A, R15.1, R17.1, U$2.8 (VDD)
POS_6V: C3.1, C7.1, IC7.3 (VO), TL082D-1.8 (V+), TL082D-2.8 (V+), U$1.6 (V+), U$4.6 (V+)
POS_12V: F1.2, IC1.3 (VO), IC2.1 (VI), IC7.1 (VI)
RESET: S1.2 (S), U1.RES
RS: R42.1, TFT01-3.2.7
RST: R21.2, TFT01-3.2.33
SD_CS: R59.2, TFT01-3.2.36, U1.D53
SD_DIN: R58.2, TFT01-3.2.34
SD_IN: U1.D51, U$2.1 (DIN)
SD_OUT: R45.2, TFT01-3.2.30
SD_SCK: R57.2, TFT01-3.2.32, U1.D52, U$2.2 (SCLK)
T2_5: U$4.5 (V-)
VCC: JP6.2, JP6.4, JP6.6, R20.1, TFT01-3.2.3, U1.5V@0 (5V), U1.5V@1 (5V), U1.5V@2 (5V), U$8.VDD
WR: R43.1, TFT01-3.2.9
X_IN: R18.1, TL082D-1.1 (OUT), U$1.4 (IN)
Y_IN: R19.1, TL082D-2.1 (OUT), U$4.4 (IN)
Z-DIR: U1.D14, U$8.DIR
Z-EN: R20.2, U1.A8, U$8.EN
Z-MAX: U1.D17, ZMAX.1
Z-MIN: U1.D16, ZMIN.1
Z-STEP: U1.D15, U$8.STEP

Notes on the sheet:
X-Pos
X-Neg
Y-Pos
Y-Neg
Pos 15V from PS
Neg 15V from PS
GND from PS

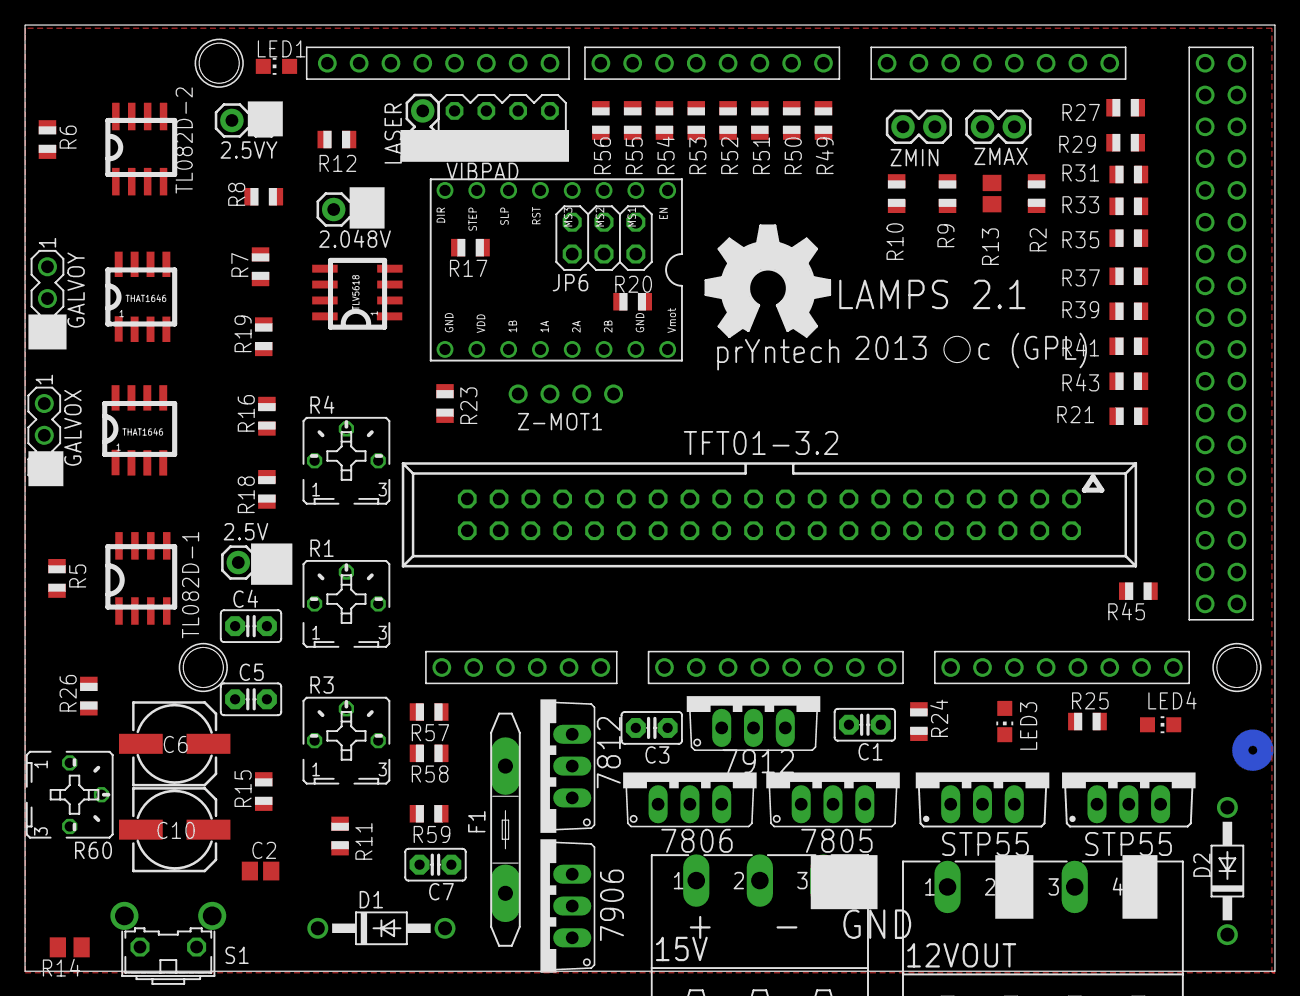
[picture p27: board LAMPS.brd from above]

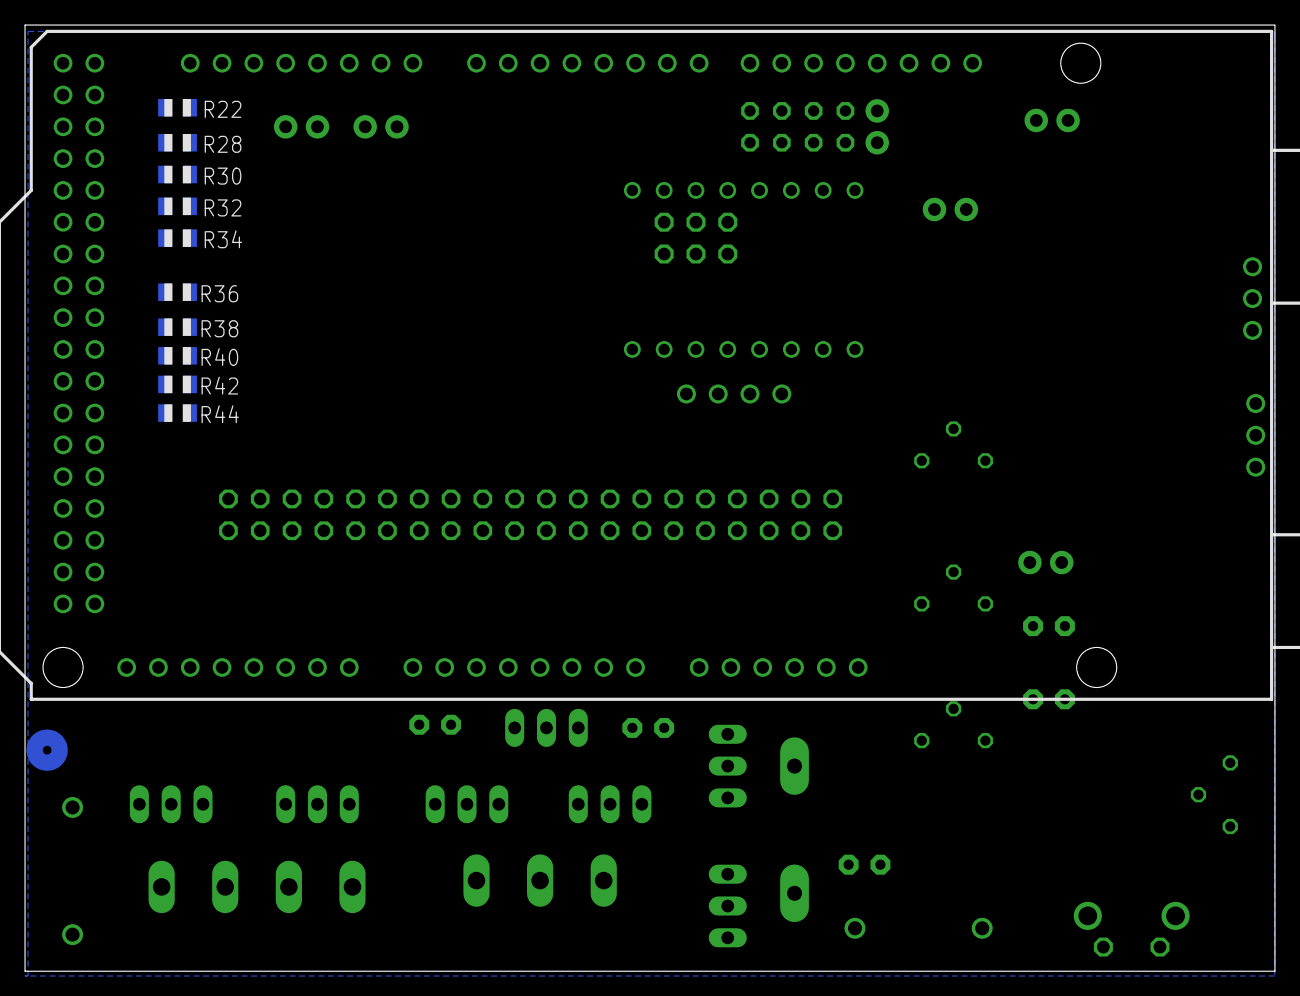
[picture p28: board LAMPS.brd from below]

Board: 2 copper layers, 99.8 x 75.6 mm, 101 parts (10 on the bottom side), 126 nets.

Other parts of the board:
U$3: OSHW_FILLX350_NOTEXT

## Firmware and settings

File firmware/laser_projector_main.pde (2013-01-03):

#include "Spi.h"

#define SCK_PIN 13   // Clock
#define MISO_PIN 12
#define MOSI_PIN 11
#define SS_PIN 10    // Control Signal
#define laserEn 9    // laser enable signal

//------ Controls -------------------------
int OffsetX = 4095;
int OffsetY = 0;
int textSpeed = 15;
int windowX = 0;
int minWindow = 600;
int maxWindow = 3800;
int prevX = 0;
int scaleY = 1;
int scaleX = 1;

void setup()
{
  Serial.begin(9600);
  pinMode(laserEn, OUTPUT);
  SPCR = (1<<SPE)|(1<<MSTR)|(1<<CPHA);
  //clr=SPSR;
  //clr=SPDR;
  delay(10);
  setCoords(2048,2048,0);    // setCoords(x, y, laserEn);
}

void loop()
{
  for (OffsetX = -4000; OffsetX < 12000; OffsetX++)
  {
    OffsetX = OffsetX + textSpeed;
    // Merry
setCoords(0,2159,0);
setCoords(0,2159,0);
setCoords(0,2159,0);
setCoords(0,2159,0);
setCoords(0,2159,0);
setCoords(0,2159,0);
setCoords(0,2159,0);
setCoords(0,2159,0);
setCoords(0,2159,0);
setCoords(0,2159,0);
setCoords(0,2159,1);
setCoords(84,2271,1);
setCoords(156,2335,1);
setCoords(204,2335,1);
setCoords(156,2255,1);
setCoords(84,2143,1);
setCoords(0,1984,1);
setCoords(72,2079,1);
setCoords(180,2207,1);
setCoords(276,2319,1);
setCoords(300,2271,1);
setCoords(228,2175,1);
setCoords(132,2016,1);
setCoords(264,2175,1);
setCoords(396,2335,1);
setCoords(432,2367,1);
setCoords(396,2239,1);
setCoords(324,2143,1);
setCoords(252,2016,1);
setCoords(276,1984,1);
setCoords(396,2048,1);
setCoords(468,2079,1);
setCoords(468,2143,1);
setCoords(420,2143,1);
setCoords(384,2095,1);
setCoords(372,2016,1);
setCoords(420,1984,1);
setCoords(516,2063,1);
setCoords(564,2159,1);
setCoords(540,2127,1);
setCoords(588,2111,1);
setCoords(540,2048,1);
setCoords(528,2000,1);
setCoords(588,2032,1);
setCoords(660,2111,1);
setCoords(672,2159,1);
setCoords(660,2111,1);
setCoords(708,2111,1);
setCoords(672,2048,1);
setCoords(660,2000,1);
setCoords(732,2032,1);
setCoords(804,2143,1);
setCoords(780,2016,1);
setCoords(804,2016,1);
setCoords(900,2143,1);
setCoords(816,1984,1);
setCoords(744,1872,1);
setCoords(684,1824,1);
setCoords(684,1904,1);
setCoords(756,1952,1);
setCoords(888,2000,1);
setCoords(888,2000,0);

// Christmas
setCoords(1536,2335,0);
setCoords(1536,2335,0);
setCoords(1536,2335,0);
setCoords(1536,2335,0);
setCoords(1536,2335,0);
setCoords(1536,2335,0);
setCoords(1536,2335,1);
setCoords(1464,2303,1);
setCoords(1416,2239,1);
setCoords(1416,2175,1);
setCoords(1512,2271,1);
setCoords(1512,2399,1);
setCoords(1428,2351,1);
setCoords(1320,2287,1);
setCoords(1224,2175,1);
setCoords(1200,2016,1);
setCoords(1284,1984,1);
setCoords(1392,2048,1);
setCoords(1476,2111,1);
setCoords(1584,2207,1);
setCoords(1656,2351,1);
setCoords(1560,2175,1);
setCoords(1488,2048,1);
setCoords(1464,2016,1);
setCoords(1560,2095,1);
setCoords(1608,2127,1);
setCoords(1584,2079,1);
setCoords(1524,2016,1);
setCoords(1584,2016,1);
setCoords(1656,2079,1);
setCoords(1704,2159,1);
setCoords(1680,2127,1);
setCoords(1728,2111,1);
setCoords(1680,2079,1);
setCoords(1668,2000,1);
setCoords(1752,2048,1);
setCoords(1990,2239,1);
setCoords(1924,2143,1);
setCoords(1824,2143,0);
setCoords(1824,2143,0);
setCoords(1824,2143,0);
setCoords(1776,2048,1);
setCoords(1776,2048,0);
setCoords(1776,2048,0);
setCoords(1776,2048,0);
setCoords(1824,2143,1);
setCoords(1824,2143,1);
setCoords(1788,1984,1);
setCoords(1848,2032,1);
setCoords(1944,2143,1);
setCoords(1944,2048,1);
setCoords(1896,2016,1);
setCoords(1848,2016,1);
setCoords(1944,2016,1);
setCoords(2063,2111,1);
setCoords(2135,2255,1);
setCoords(2087,2207,1);
setCoords(2004,2175,1);
setCoords(2063,2175,1);
setCoords(2159,2175,1);
setCoords(2111,2175,1);
setCoords(2063,2143,1);
setCoords(2016,2048,1);
setCoords(2040,2000,1);
setCoords(2111,2063,1);
setCoords(2183,2127,1);
setCoords(2135,2063,1);
setCoords(2111,2016,1);
setCoords(2207,2127,1);
setCoords(2231,2111,1);
setCoords(2195,2048,1);
setCoords(2159,1984,1);
setCoords(2219,2095,1);
setCoords(2279,2143,1);
setCoords(2303,2111,1);
setCoords(2255,2063,1);
setCoords(2231,2016,1);
setCoords(2291,2016,1);
setCoords(2267,1984,1);
setCoords(2303,2016,1);
setCoords(2351,2079,1);
setCoords(2411,2143,1);
setCoords(2459,2095,1);
setCoords(2375,2079,1);
setCoords(2339,2016,1);
setCoords(2375,2016,1);
setCoords(2423,2048,1);
setCoords(2447,2111,1);
setCoords(2447,2143,1);
setCoords(2423,2048,1);
setCoords(2411,1984,1);
setCoords(2435,2000,1);
setCoords(2363,2016,1);
setCoords(2447,2000,1);
setCoords(2531,2079,1);
setCoords(2591,2143,1);
setCoords(2567,2048,1);
setCoords(2519,2016,1);
setCoords(2471,2016,1);
setCoords(2543,1984,1);
setCoords(2639,2016,1);
setCoords(2690,2016,1);

// from
setCoords(2939,1984,0);
setCoords(2939,1984,0);
setCoords(2939,1984,0);
setCoords(2939,1984,0);
setCoords(2939,1984,0);
setCoords(2939,1984,1);
setCoords(3035,2079,1);
setCoords(3131,2207,1);
setCoords(3203,2303,1);
setCoords(3227,2335,1);
setCoords(3155,2271,1);
setCoords(3083,2175,1);
setCoords(3035,2048,1);
setCoords(2975,1888,1);
setCoords(2963,1792,1);
setCoords(2987,1824,1);
setCoords(3035,1888,1);
setCoords(3059,1968,1);
setCoords(3083,2048,1);
setCoords(3059,2063,1);
setCoords(3023,2016,1);
setCoords(3059,1984,1);
setCoords(3167,2048,1);
setCoords(3215,2175,1);
setCoords(3191,2111,1);
setCoords(3251,2111,1);
setCoords(3239,2079,1);
setCoords(3191,2016,1);
setCoords(3203,1984,1);
setCoords(3275,2063,1);
setCoords(3419,2111,1);
setCoords(3299,2048,1);
setCoords(3287,1984,1);
setCoords(3335,1984,1);
setCoords(3371,2032,1);
setCoords(3383,2079,1);
setCoords(3299,2127,1);
setCoords(3299,2079,1);
setCoords(3347,2048,1);
setCoords(3383,2000,1);
setCoords(3443,2048,1);
setCoords(3491,2127,1);
setCoords(3479,2079,1);
setCoords(3443,1984,1);
setCoords(3491,2048,1);
setCoords(3515,2111,1);
setCoords(3563,2095,1);
setCoords(3515,2032,1);
setCoords(3479,1984,1);
setCoords(3539,2048,1);
setCoords(3587,2111,1);
setCoords(3635,2111,1);
setCoords(3611,2079,1);
setCoords(3587,2032,1);
setCoords(3563,1984,1);
setCoords(3599,1984,1);
setCoords(3599,1984,0);

// the
setCoords(3935,1984,0);
setCoords(3935,1984,0);
setCoords(3935,1984,0);
setCoords(3935,1984,0);
setCoords(3935,1984,0);
setCoords(3935,1984,1);
setCoords(4007,2048,1);
setCoords(4091,2143,1);
setCoords(4175,2399,1);
setCoords(4115,2143,1);
setCoords(4019,2143,1);
setCoords(4103,2143,1);
setCoords(4175,2127,1);
setCoords(3959,2143,1);
setCoords(4079,2063,1);
setCoords(4055,1984,1);
setCoords(4127,2016,1);
setCoords(4223,2143,1);
setCoords(4307,2271,1);
setCoords(4343,2335,1);
setCoords(4295,2287,1);
setCoords(4211,2127,1);
setCoords(4151,1984,1);
setCoords(4235,2095,1);
setCoords(4295,2111,1);
setCoords(4247,2048,1);
setCoords(4223,2000,1);
setCoords(4295,2016,1);
setCoords(4379,2048,1);
setCoords(4415,2111,1);
setCoords(4391,2143,1);
setCoords(4343,2095,1);
setCoords(4319,2016,1);
setCoords(4343,1984,1);
setCoords(4403,1984,1);
setCoords(4343,1984,1);
setCoords(4390,1984,1);

// Hardware
setCoords(4955,2319,0);
setCoords(4955,2319,0);
setCoords(4955,2319,0);
setCoords(4955,2319,0);
setCoords(4955,2319,0);
setCoords(4955,2319,1);
setCoords(5027,2367,1);
setCoords(5099,2367,1);
setCoords(5051,2303,1);
setCoords(4955,2143,1);
setCoords(4883,2048,1);
setCoords(4763,1952,1);
setCoords(4715,2048,1);
setCoords(4799,2111,1);
setCoords(4907,2143,1);
setCoords(5063,2159,1);
setCoords(5123,2175,1);
setCoords(5111,2207,1);
setCoords(5171,2303,1);
setCoords(5219,2367,1);
setCoords(5147,2255,1);
setCoords(5039,2079,1);
setCoords(4991,2016,1);
setCoords(5051,1984,1);
setCoords(5135,2063,1);
setCoords(5195,2111,1);
setCoords(5267,2095,1);
setCoords(5171,2079,1);
setCoords(5147,2016,1);
setCoords(5171,2016,1);
setCoords(5219,2048,1);
setCoords(5243,2095,1);
setCoords(5231,2143,1);
setCoords(5219,2079,1);
setCoords(5219,2016,1);
setCoords(5255,2016,1);
setCoords(5291,2095,1);
setCoords(5351,2175,1);
setCoords(5339,2143,1);
setCoords(5387,2111,1);
setCoords(5363,2111,1);
setCoords(5339,2048,1);
setCoords(5339,1984,1);
setCoords(5411,2016,1);
setCoords(5435,2095,1);
setCoords(5471,2127,1);
setCoords(5543,2127,1);
setCoords(5447,2095,1);
setCoords(5411,2032,1);
setCoords(5459,2016,1);
setCoords(5507,2048,1);
setCoords(5579,2175,1);
setCoords(5675,2303,1);
setCoords(5627,2271,1);
setCoords(5555,2175,1);
setCoords(5531,2095,1);
setCoords(5507,1984,1);
setCoords(5579,2032,1);
setCoords(5663,2143,1);
setCoords(5651,2079,1);
setCoords(5615,2016,1);
setCoords(5651,2016,1);
setCoords(5699,2079,1);
setCoords(5723,2143,1);
setCoords(5687,2079,1);
setCoords(5687,2016,1);
setCoords(5735,2032,1);
setCoords(5783,2111,1);
setCoords(5747,2127,1);
setCoords(5735,2048,1);
setCoords(5747,1984,1);
setCoords(5795,2048,1);
setCoords(5831,2111,1);
setCoords(5915,2143,1);
setCoords(5927,2095,1);
setCoords(5843,2095,1);
setCoords(5795,2016,1);
setCoords(5855,2016,1);
setCoords(5903,2079,1);
setCoords(5915,2111,1);
setCoords(5867,2032,1);
setCoords(5903,2000,1);
setCoords(5963,2048,1);
setCoords(5999,2095,1);
setCoords(6011,2175,1);
setCoords(6011,2143,1);
setCoords(6011,2111,1);
setCoords(6047,2111,1);
setCoords(6035,2079,1);
setCoords(5987,2016,1);
setCoords(6011,2000,1);
setCoords(6107,2048,1);
setCoords(6202,2095,1);
setCoords(6178,2143,1);
setCoords(6095,2079,1);
setCoords(6083,2048,1);
setCoords(6131,1984,1);
setCoords(6358,2000,1);
setCoords(6358,2000,1);

// Group
setCoords(7030,2351,0);
setCoords(7030,2351,0);
setCoords(7030,2351,0);
setCoords(7030,2351,0);
setCoords(7030,2351,1);
setCoords(6958,2303,1);
setCoords(6970,2239,1);
setCoords(7042,2287,1);
setCoords(7066,2367,1);
setCoords(6982,2399,1);
setCoords(6838,2287,1);
setCoords(6730,2175,1);
setCoords(6706,2048,1);
setCoords(6778,2032,1);
setCoords(6898,2095,1);
setCoords(6982,2191,1);
setCoords(7006,2207,1);
setCoords(6922,2095,1);
setCoords(6874,1984,1);
setCoords(6790,1888,1);
setCoords(6706,1856,1);
setCoords(6658,1856,1);
setCoords(6694,1952,1);
setCoords(6778,2016,1);
setCoords(6874,2016,1);
setCoords(6946,2016,1);
setCoords(7018,2048,1);
setCoords(7066,2175,1);
setCoords(7042,2127,1);
setCoords(7090,2127,1);
setCoords(7066,2079,1);
setCoords(7042,2016,1);
setCoords(7114,2032,1);
setCoords(7150,2079,1);
setCoords(7234,2143,1);
setCoords(7162,2048,1);
setCoords(7162,2016,1);
setCoords(7222,2048,1);
setCoords(7234,2111,1);
setCoords(7210,2143,1);
setCoords(7174,2095,1);
setCoords(7210,2048,1);
setCoords(7258,2016,1);
setCoords(7282,2079,1);
setCoords(7342,2143,1);
setCoords(7306,2079,1);
setCoords(7306,1984,1);
setCoords(7354,2048,1);
setCoords(7402,2127,1);
setCoords(7354,2048,1);
setCoords(7354,2016,1);
setCoords(7402,2016,1);
setCoords(7450,2079,1);
setCoords(7522,2143,1);
setCoords(7522,2143,1);
setCoords(7474,2079,1);
setCoords(7450,2016,1);
setCoords(7402,1936,1);
setCoords(7354,1872,1);
setCoords(7378,1920,1);
setCoords(7426,1984,1);
setCoords(7498,2079,1);
setCoords(7546,2111,1);
setCoords(7570,2111,1);
setCoords(7570,2079,1);
setCoords(7546,2032,1);
setCoords(7498,2016,1);
setCoords(7474,2032,1);
setCoords(7522,2016,1);
setCoords(7570,2000,1);
setCoords(7630,2048,1);
setCoords(7630,2048,0);
}

}

void setCoords(int x, int y, boolean Las_EN)
{
  x = (x*scaleX) - OffsetX;
  y = (y*scaleY) - OffsetY;
  if (x > 0 && x < 4095)
  {
  if (x < minWindow || x > maxWindow)
  {
    digitalWrite(laserEn, LOW);
  }
  else
  {
  digitalWrite(laserEn, Las_EN);
  }
  // Run the send coords cycles twice to get the TLV5618 to take
  digitalWrite(SS_PIN, LOW);
  Spi.transfer((0x5*16)|(x/256));
  Spi.transfer(x & 0xFF);
  digitalWrite(SS_PIN, HIGH);
  digitalWrite(SS_PIN, LOW);
  Spi.transfer((0x5*16)|(x/256));
  Spi.transfer(x & 0xFF);
  digitalWrite(SS_PIN, HIGH);
  digitalWrite(SS_PIN, LOW);
  Spi.transfer((0xC*16)|(y/256));
  Spi.transfer(y & 0xFF);
  digitalWrite(SS_PIN, HIGH);
  digitalWrite(SS_PIN, LOW);
  Spi.transfer((0xC*16)|(y/256));
  Spi.transfer(y & 0xFF);
  digitalWrite(SS_PIN, HIGH);
  //delayMicroseconds(2);
  }
  else
  {
  digitalWrite(laserEn, 0);
  //delayMicroseconds(15);
  }
}

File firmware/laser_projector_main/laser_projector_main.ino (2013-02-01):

#include <SPI.h>
#include <math.h>

//------------------------------
// DAC Data Transfer
#define SLAVESELECT 53 // CS
#define DATAOUT 51 // DIN
#define SPICLOCK 52 // SCLK
//-------------------------------

#define laserEn 31    // laser enable signal
#define fanEn 10    // laser enable signal

//------ Controls -------------------------
int OffsetX = 0;
int OffsetY = 0;
int textSpeed = 15;
int windowX = 0;
int minWindow = 600;
int maxWindow = 3800;
int prevX = 0;
int scaleY = 1;
int scaleX = 1;

#ifdef WIBLOCKS
SPI spi(SPI_TIMEOUT, NB1A_MOSI_PIN, NB1A_MISO_PIN, NB1A_SCK_PIN);
DAC_TLV5618 dac(SS_PIN, DAC_NORMAL, DAC_FAST);
#endif

void setup()
{
  Serial.begin(9600);
  pinMode(laserEn, OUTPUT);
  pinMode(fanEn, OUTPUT);

  pinMode(DATAOUT, OUTPUT);
  pinMode(SPICLOCK,OUTPUT);
  pinMode(SLAVESELECT,OUTPUT);
  SPI.begin();
  delay(10);
}

/////////////////////////////////////////////////////////////////////
// DAC SPI Interface
char spi_transfer(volatile char data)
{
SPDR = data; // Start the transmission
while (!(SPSR & (1<<SPIF))) // Wait the end of the transmission
{
};
return SPDR; // return the received byte
}

//----------------------------------------------------------------------------------------------------------
//----------------------- TLV5618 FUNCTION -----------------------------------------------------
//----------------------------------------------------------------------------------------------------------
//----------------------------------------------------------------------------------------------------------
void TLV5618_out(double A, double B){
  byte prev_SPCR = SPCR;                                           // save the previous SPI settings
  SPCR = (1<<SPE)|(1<<MSTR)|(1<<CPHA);                             // setup SPI for the DAC
  unsigned int chA = A;
  unsigned int chB = B;
  spi_transfer(2, chB);
  spi_transfer(2, chB);
  spi_transfer(1, chA);
  spi_transfer(1, chA);
  SPCR = prev_SPCR;                                                // restore the previous SPI settings
}

void spi_transfer(int channel, unsigned int data){
  digitalWrite(SLAVESELECT, LOW);
  delayMicroseconds(10);
  if (channel == 1) SPI.transfer((0xC*16)|(data/256));             // output from channel A (1)
  if (channel == 2) SPI.transfer((0x5*16)|(data/256));             // output from channel B (2)
  SPI.transfer(data & 0xFF);
  delayMicroseconds(10);
  digitalWrite(SLAVESELECT, HIGH);
}
//--------------------------------------------------- END FUNCTION -------------------------------------------------------

void loop()
{ 
  //return;
  
  int maxv = 4028;
  int inca = 10;
  int del = 8;
  int ldel = 2;
  int repeat = 2;
//  delay(5);
  digitalWrite(fanEn,1);
  
  int squareheight = 600; //4094
  int line_gain = 10;

   int minv=600;
   
   digitalWrite(laserEn,1);
   
   setCoords(0,0);  
     
   delay(3000);
   
   setCoords(2048,2048);  
   
   delay(3000);
   
   setCoords(4095,4095);  
   
   delay(3000);
   
   for(int i = minv; i < 4096; i+=inca)
   {
     setCoords(i,i);  
   }
   
   for(int i = 1; i < 4096-minv; i+=inca)
   {
     setCoords(4095-i,4095-i);  
   }

}

void setCoords(int x, int y)
{
  delay(5);
  TLV5618_out(x,y);
}

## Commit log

2012-11-07 Initial Add of Board
    [ArduinoMEGAReferenceShield.brd, ArduinoMEGAReferenceShield.sch]
2012-11-07 Add Laser
    [ArduinoMEGAReferenceShield.sch]
2012-11-07 Clean up
    [ArduinoMEGAReferenceShield.brd, ArduinoMEGAReferenceShield.sch, LAMPS.brd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]
2012-11-08 add ground
2012-11-08 some image buildup
    [LAMPS.brd]
2012-11-08 resistors on AD420, 3 pin galvo
    [LAMPS - Copy.brd, LAMPS - Copy.sch]
2012-11-09 More work...
    [LAMPS.brd, LAMPS.sch]
2012-11-12 Switching AD420 Chip mount
    [LAMPS.brd, LAMPS.sch]
2012-11-13 Remove expensive component for DIY variety
    [LAMPS.brd, LAMPS.sch]
2012-11-21 Some pcb work... adding in new schematic
    [LAMPS.brd, LAMPS.sch, RAMPS_1-41.sch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]
2012-11-27 Add Lamps board
    [LAMPS_1-41.brd, LAMPS_1-41.sch, RAMPS_1-41.brd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]
2012-11-27 Start relaying board
    [LAMPS_1-41.brd]
2012-11-28 Shuffle Board, Gen Gerbers
    [LAMPS_1-41.brd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]
2012-11-28 LAMPS 1.0 GERBERS
    [LAMPS_1-41.brd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]
2012-11-29 Clean-Up, Add Top Z Mount
    [2020_foot.stl, LAMPS.brd, LAMPS.sch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]
2012-11-30 Add Bottom Mount
    [z_bottom_mount.skp]
2012-12-02 Add stage mount, clean up top mount
    [platform_mount.skp, platform_mount.stl, platform_mount_fixed.stl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]
2012-12-02 Add mount
    [build_platform_connector.skp, build_platform_connector.stl]
2012-12-02 Cleanup of Repo
    [LAMPS.brd, LAMPS.sch]
2012-12-02 FUll Rendering
    [LAMPS_full_model.skp]
2012-12-03 Add Platform dxf files
    [LAMPS_full_model.skp, bottom_platform.dxf, top_platform.dxf]
2012-12-04 Add Build Platform brd
    [buildPlatform.brd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]
2012-12-05 Add Build Platform (Ordered)
    [buildPlatform.GBL, buildPlatform.GBO, buildPlatform.GBS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]
2012-12-13 Add Vat Mount
    [LAMPS_full_model.skp, vibrating_vat_mount.skp, vibrating_vat_mount.stl]
2012-12-13 Update vat mount
    [buildPlatform.brd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]
2012-12-14 Added acrylic vat design
    [LAMPS_full_model.skp, acrylic_vat.skp, vibrating_vat_mount.skp]
2012-12-15 cleanup lamps skp
    [LAMPS_full_model.skp]
2012-12-16 Updated vat and mount
    [LAMPS_full_model.skp, vibrating_vat_mount.stl]
2012-12-16 added laser etch for resin level to vat front
    [LAMPS_full_model.skp, vibrating_vat_mount.stl]
2012-12-16 updated lamps model
    [LAMPS_full_model.skp]
2012-12-20 Making strides
    [LAMPS.csv, LAMPS.sch, vibrating_vat_mount.stl]
2012-12-28 Add some changes I've been sitting on
    [LAMPS_full_model.skp]
2013-01-03 Some Laser Wurk
2013-01-11 Add updated Build Platform and Lamps 2.1 Sch
    [LAMPS.brd, LAMPS.sch, buildPlatform.brd]
2013-01-12 Case Template
    [fan_mount.skp, fan_mount.stl]
2013-01-14 Added case files
2013-01-14 Few updats
    [front.dxf, front_2.dxf]
2013-01-14 This thing is purty
    [back.dxf, back.skp, front.dxf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]
2013-01-15 Update README.md
    Added Resistance for new pair of galvo drivers
2013-01-15 Nightly Commit ... laser moves much better... more work to be done on planner
    [LAMPS.brd, LAMPS.sch]
2013-01-17 Updates to 2.1 Board
    [LAMPS.brd, LAMPS.sch]
2013-01-21 Update Case Design
    [back.dxf, bottom_platform.dxf, front_LCD.dxf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]
2013-01-23 Add Endstops
    [build_platform_connector.stl, endstopholder_fixed.stl]
2013-01-27 Update README.md
    Switch lisencse
2013-01-27 Updated boards
    [LAMPS.brd, LAMPS.sch]
2013-01-28 Clean up parts directory... prepare to generate clean, good stl files
    [2020_foot.stl, back.skp, bottom_platform.dxf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]
2013-01-28 Exported stl files
    [Build_Platform.stl, Laser_Mount.stl, Mirror_Mount.stl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]
2013-01-28 Clean Up Repository
    [24by48_sheet.dxf, LAMPS.brd, LAMPS.csv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]
2013-01-29 Everyone loves a good rendering.
    [clear_front_door_window.dxf, clear_side_window.dxf, clear_side_window_two.dxf]
2013-02-14 Updated Vat
    [vat_back.dxf, vat_bottom.dxf, vat_front.dxf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]
2013-02-19 Added LASER mount with IRIS Mount
    [Laser_Mount_Iris.stl]
2013-02-28 Added some test files, cleaned up some stl
    [Z_Axis_Platform_Mount.stl, vat_adherence_30mm_square.stl]
2013-03-05 Added OpenSL 1.0 Board and stencil
    [EiffelTower_top.stl, Mirror_Mount.stl, Z_Axis_Bottom.stl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]
2013-03-06 Added BOM and PDF for board layout
2013-03-25 Test Firmware and updated parts
    [platform_base.stl, platform_head.stl, vat_bottom_test.dxf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]
2013-03-27 Updated Mounts
2013-04-01 Added Laser Cut Laser and Iris Mount
    [laser_mount_1.dxf, laser_mount_2.0.stl, laser_mount_2.dxf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]
2013-04-11 Updates for bottom
    [laser_mount_1.dxf, laser_mount_2.dxf, laser_mount_3.dxf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]
2013-04-13 Added fab files
    [bittele_bom.xls, bom.xls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]
2013-04-18 Added a few files
    [vat_mount_new.dxf, vat_mount_new.skp, vat_mount_new.stl]
2013-06-05 Added DXF and PLT files
    [bottom_platform.DXF, laser_mount.DXF, top_platform.DXF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]
2013-06-12 Clean Up Repo -- Add SVG and PDF for Laser Cut
    [Build_Platform.stl, EiffelTower_top.stl, LAMPS.brd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]
2013-08-21 Add raw wiring diagram
2016-09-26 Updated repository name of Marlin fork
    It was Marlin-LAMPS but I looked around and found it to be Marlin-OpenSL. Corrected this information and submitted a Pull Request

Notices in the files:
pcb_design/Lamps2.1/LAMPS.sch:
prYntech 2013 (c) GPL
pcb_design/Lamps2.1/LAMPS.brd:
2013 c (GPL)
